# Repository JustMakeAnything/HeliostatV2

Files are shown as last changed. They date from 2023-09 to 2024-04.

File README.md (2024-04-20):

# Heliostat V2
Files for my Heliostat project. The hardware consists of an ESP32 which is connected to two stepper motors to control the azimuth and elevation of a mirror and 4 switches to detect the endpoints for the motors. Further hardware is currently not supported.

## Instructable
For details see the Instructable at:

[Instructables](https://www.instructables.com/Heliostat-Reflects-Sunlight-Inside/)

## Design

The software uses [ESPHOME](https://esphome.io/) to create the firmware. It is autonomous after it was configured especially to a specific target location (angles) where the mirror should reflect to. There is a web interface to see some values and trigger a motor calibration as well as buttons to set the target. The values are stored in the eeprom of the ESP32.

## ESPHome

These main folder is for the esphome files. Compile and upload them from the command line with:

**esphome run .\code\heliostat.yaml**

To your ESP32. See [Esphome](https://esphome.io/) for details. I haven't tested integration with home assistant. It is not needed to run the heliostat.

### Configuration

To connect to your wifi, you need to adapt the secrects.yaml. Wifi is needed to get the exact time. You can also access the web interface at heliostat.local of the given network to set the target during runtime. Otherwise use the constants.yaml to set an initial target.
There is an experimental [autocalibration](./docs/autocalibration.md) available when an additional light sensor is mounted.

## 3D Print

The STL files for 3D Print are in folder 3DPrint

There is a subfolder STL for the STL files
The folder SolidEdgeParts contains the design files for Solid Edge. Since the parts are usually exposed to the sun it makes sense to print them in a material which is more heat resistant than PLA. Especially the parts with mechanical stress like the cogweels tend to deform when in the sun. I have used transparent PETG.

### 3D Print settings

The parts can be printed with standard settings. You should rotate the parts to the flat side when slicing. Some parts like the axle and the SideNoMotor need supports.

## Electronics

Although the electronics is not complicated, you should have some experience in soldering and ideally done an ESP project before.

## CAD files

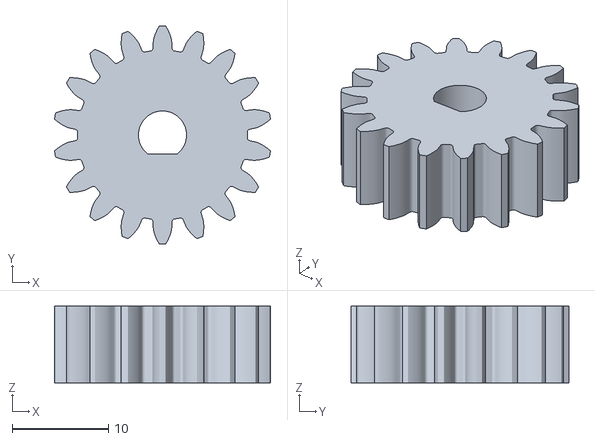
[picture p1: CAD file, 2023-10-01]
3DPrint/STL/basepinion.stl
22.5 x 22.7 x 8.00

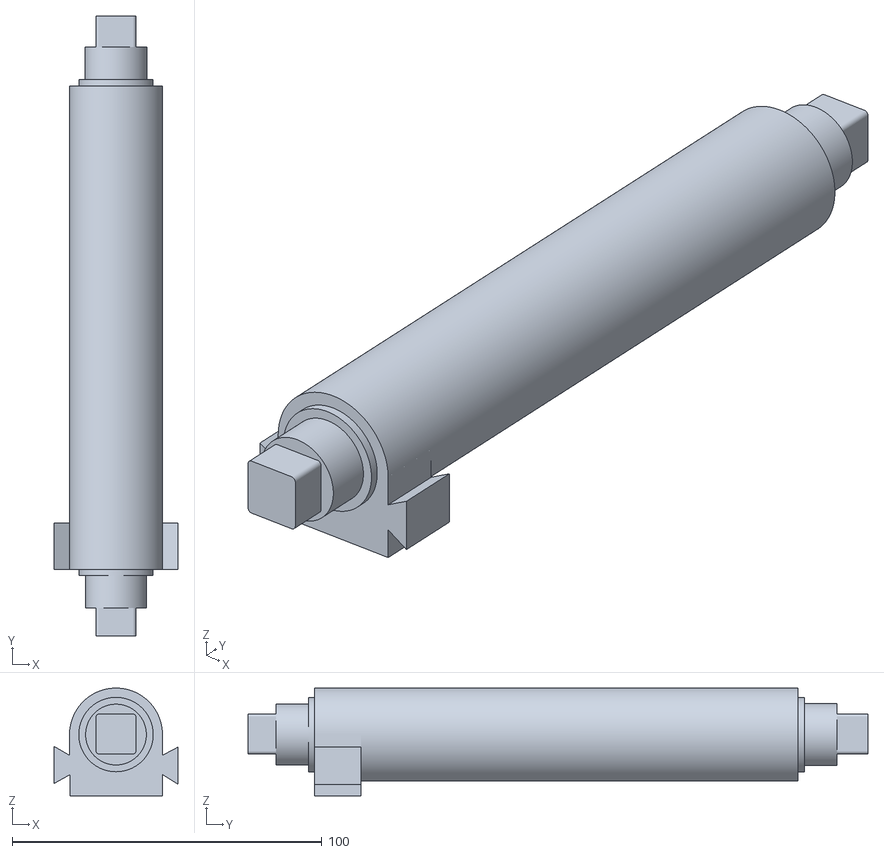
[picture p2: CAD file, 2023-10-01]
3DPrint/STL/Axle.stl
40.0 x 200.0 x 34.8

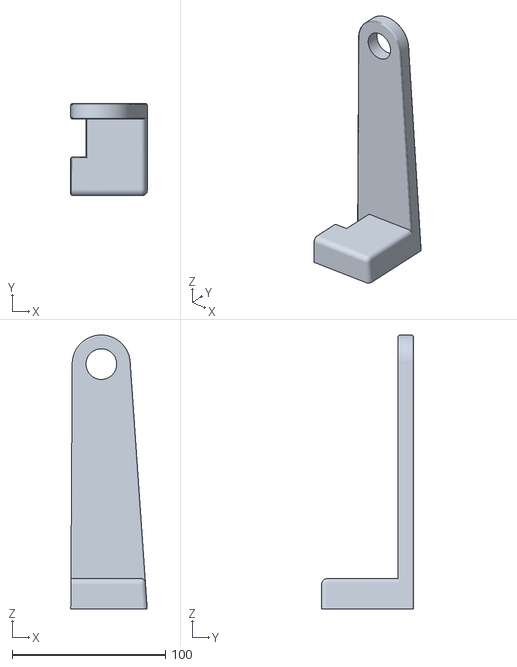
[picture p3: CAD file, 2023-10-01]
3DPrint/STL/SideNoMotor.stl
50.0 x 60.0 x 179.0

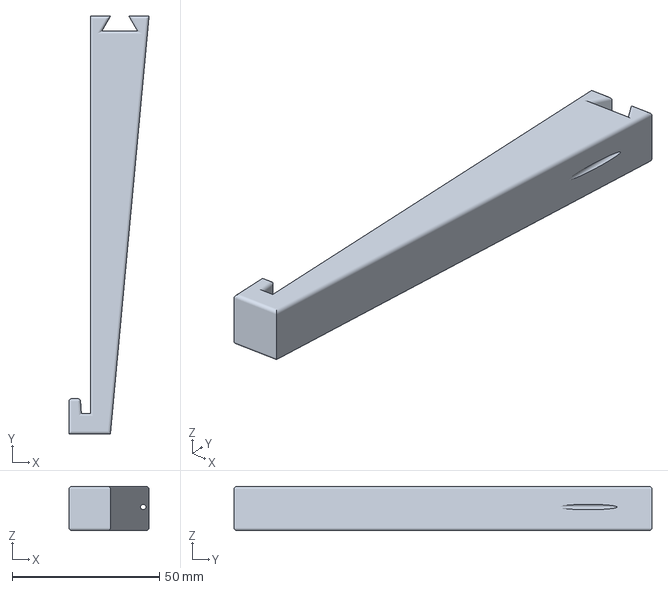
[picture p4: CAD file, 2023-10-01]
3DPrint/STL/Holder.3mf
27.3 x 142.0 x 15.0 mm

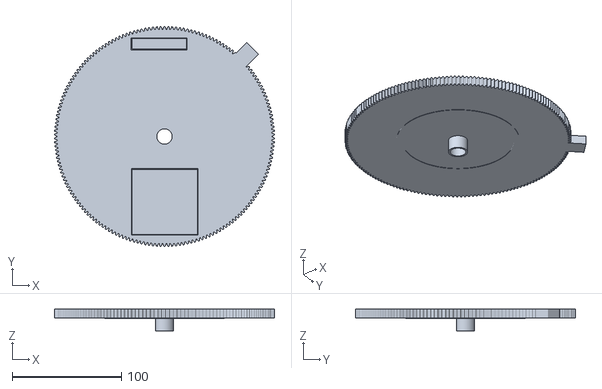
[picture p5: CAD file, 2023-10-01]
3DPrint/STL/basegear.stl
201.8 x 201.8 x 20.0

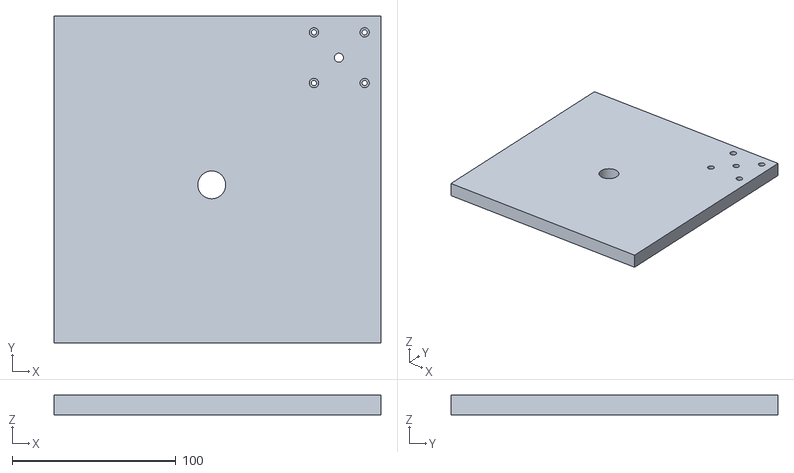
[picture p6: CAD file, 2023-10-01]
3DPrint/STL/Lid.stl
200.0 x 200.0 x 12.0

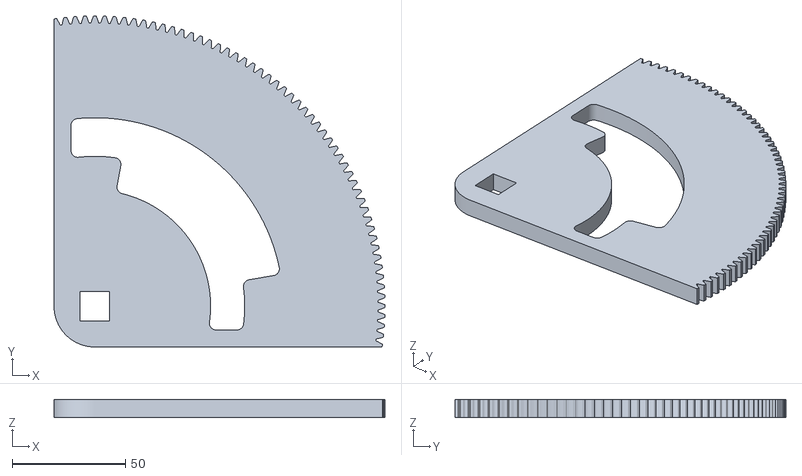
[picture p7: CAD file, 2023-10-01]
3DPrint/STL/SideGear.stl
145.8 x 145.8 x 8.00

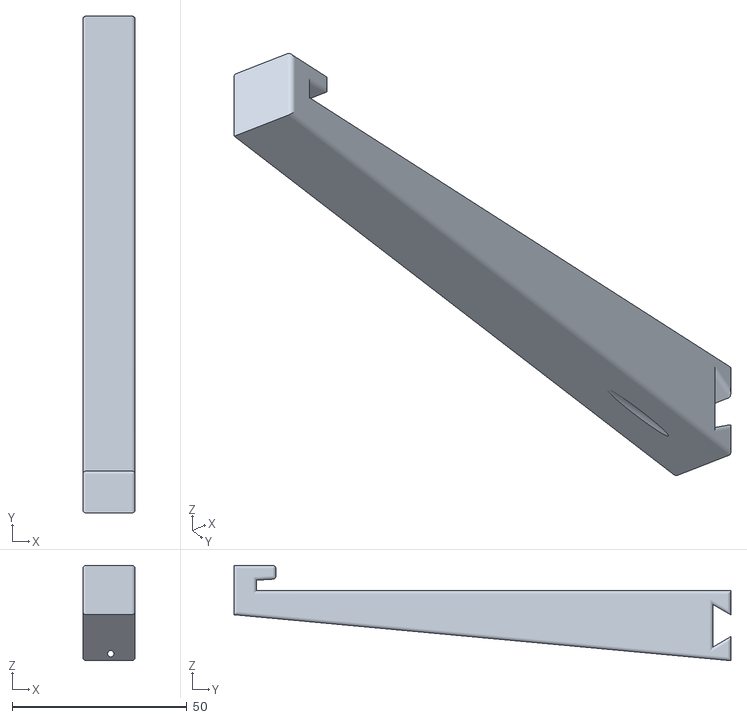
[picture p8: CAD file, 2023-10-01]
3DPrint/STL/Ausleger.stl
15.0 x 142.0 x 27.3

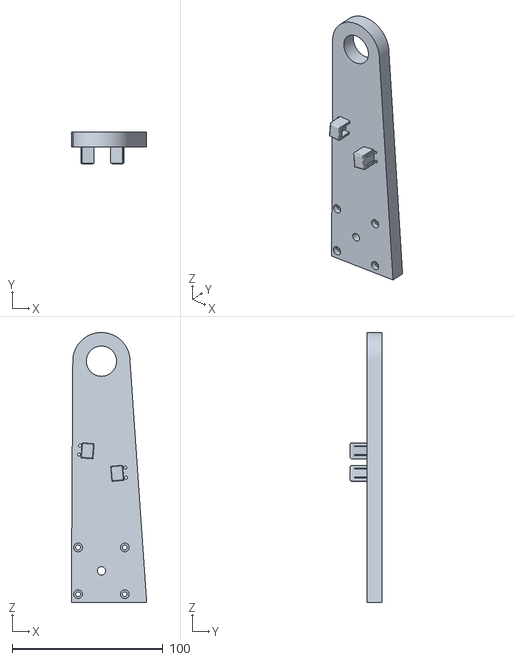
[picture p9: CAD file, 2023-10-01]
3DPrint/STL/SideMotor.stl
50.0 x 21.0 x 179.0

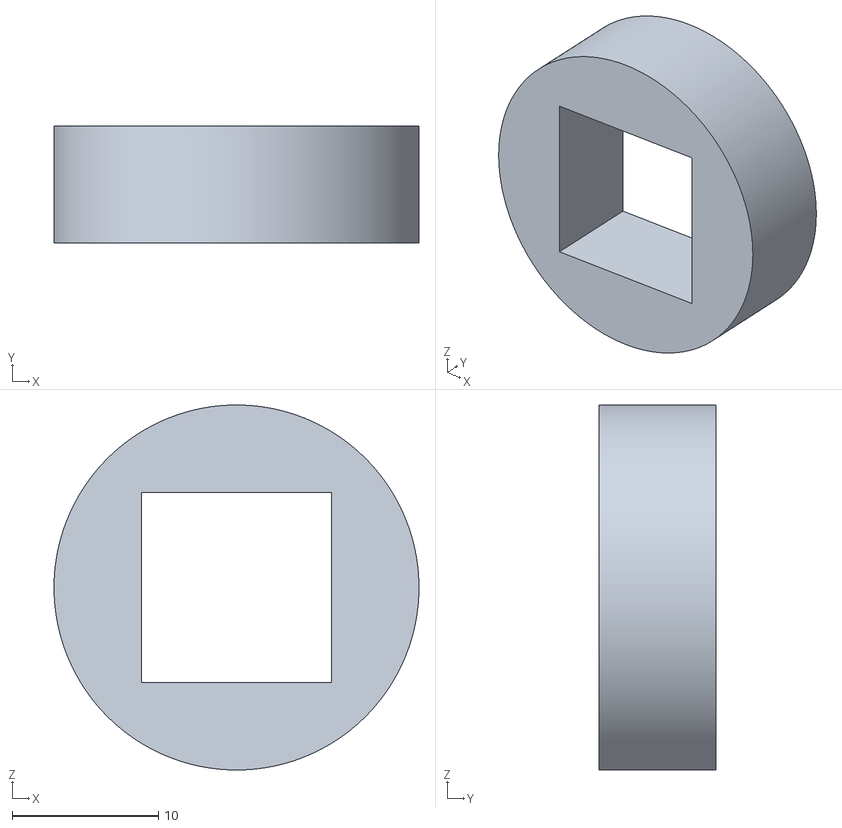
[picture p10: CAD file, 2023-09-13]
3DPrint/STL/Endplug.stl
25.0 x 8.00 x 25.0

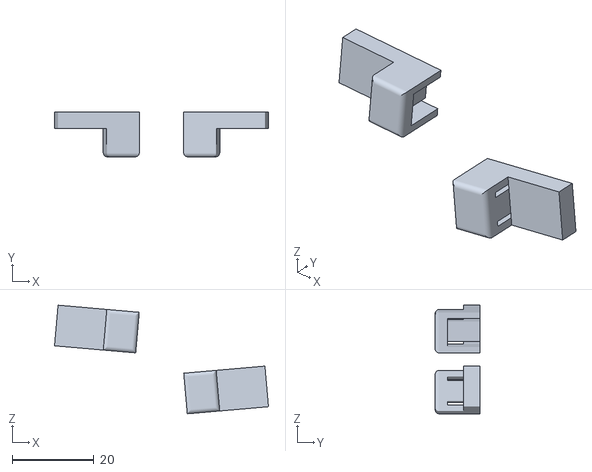
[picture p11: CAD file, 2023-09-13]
3DPrint/STL/Endstop.stl
52.5 x 11.0 x 26.6

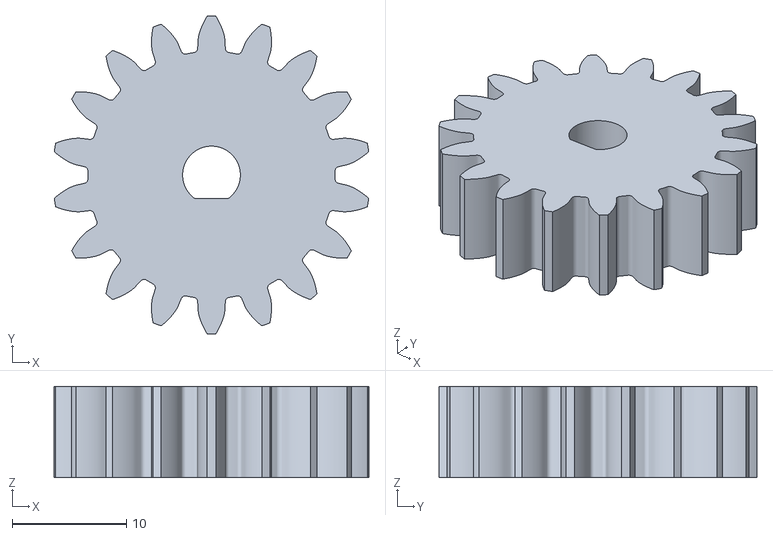
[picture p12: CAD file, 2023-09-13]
3DPrint/STL/sidepinion.stl
27.5 x 27.8 x 8.00

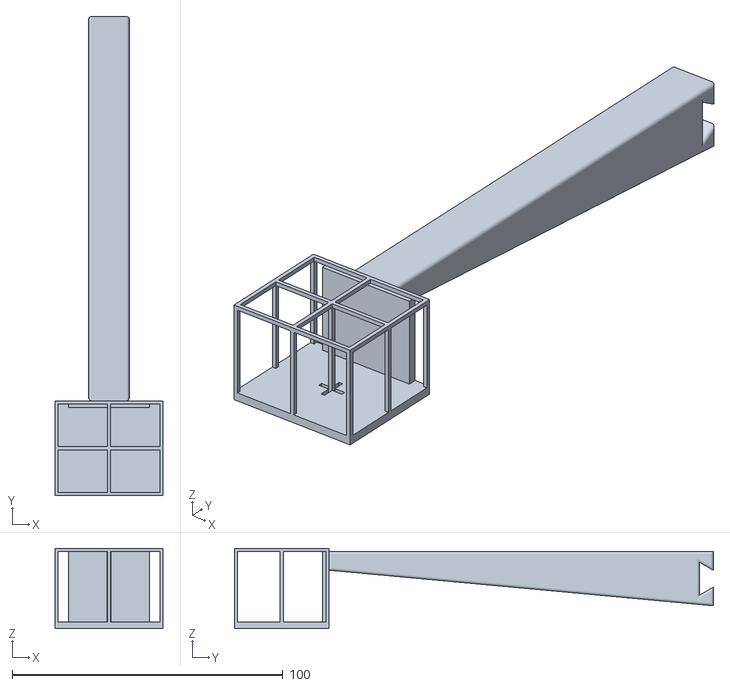
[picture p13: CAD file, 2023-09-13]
3DPrint/STL/HolderTargetSun.stl
40.0 x 177.0 x 29.6

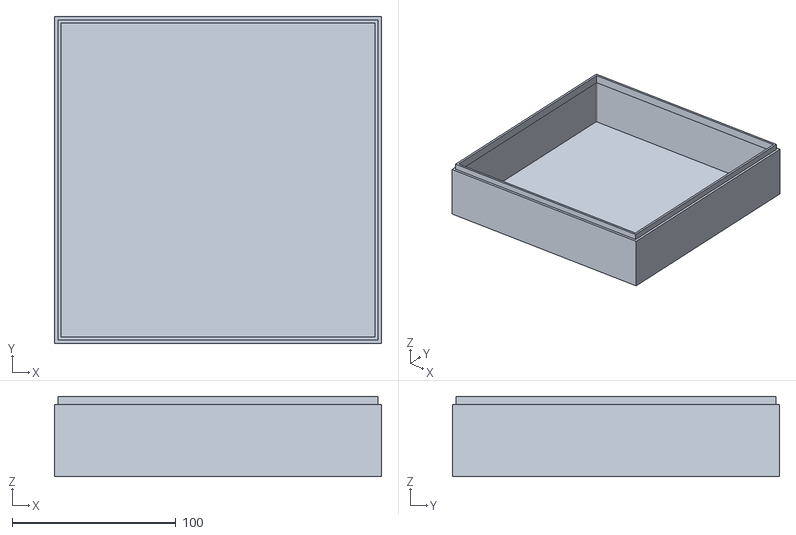
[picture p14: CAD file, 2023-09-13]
3DPrint/STL/Box.stl
200.0 x 200.0 x 49.0

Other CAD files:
3DPrint/Old/Arm.stl
3DPrint/Old/Axis.stl
3DPrint/Old/SideGear.stl
3DPrint/Old/Lid.stl
3DPrint/Old/Side1.stl
3DPrint/Old/Side2.stl
3DPrint/Old/basegear1.stl
3DPrint/Old/basepinion1.stl
3DPrint/Old/gearstopper.stl
3DPrint/STL/Holder.stl

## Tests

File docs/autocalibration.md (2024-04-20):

# Autocalibration

When a light sensor is mounted, the system can help with the calibration. Therefore the system checks if enough sunlight is available since it will not work on cloudy days due to too much ambient light and no directed light to determine a direction. A measurement is done every hour configurable in **calculations.h sunsearchdelay**

When enough light is available, the mirror and sensor is moved into the sun and tries to determine the exact direction of the sunlight. This is done by moving in a spiral around the supposed direction and measure the sunlight in the tube with the light sensor at the end. The center of the spiral also drifts in the direction where most light was measured. This process ends when the ambient sunlight falls under a certain level (no direct sunlight anymore) or the maximum search range is analyzed and no value higher than 94% of the ambient light was detected. The duration of the process is limited to 500 steps. with approx. 10 rotations. when no new measurement with a higher value is found afer 150 steps, the measurement is ended early successfully.

The direction of the maximum value is then stored as sun direction. It is stored as steps of the motors. When the three values are stored, the system attempts to calculate an adapted configuration. This will be repeated with the following measurements of the same day increasing the precision. No measurements over multiple days are stored or used. The values are shown in the log or webui.

Currently the system is not adjusting the values automatically since it is still alpha.

[12:00:56][I][measure:440]: amb: 3.069250 dir: 2.959000 saz: 0 sel: 1      driftaz -232 driftel: 20 maaz: 532 taaz: 764    az 149°
[13:38:45][I][measure:440]: amb: 2.953625 dir: 1.730625 saz: 62 sel: -85   driftaz -221 driftel: 34 maaz: 1317 taaz: 1538  az 185°
[15:19:50][I][measure:440]: amb: 2.989750 dir: 1.623750 saz: 0 sel: 1      driftaz 293 driftel:   2 maaz: 2301 taaz: 2301  az 221°
[16:59:47][I][measure:440]: amb: 2.943500 dir: 2.208625 saz: -75 sel: -103 driftaz 380 driftel: -25 maaz: 3260 taaz: 2867  az 247°

36° = 774
72° = 1537 / 2 = 769
26° = 566   * 36 / 26 = 783

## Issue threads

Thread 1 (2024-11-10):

Axel stl file issue

ecasas6, 2024-11-10:
I'm following along with your project, cool idea.  I was looking at the 3d files and it looks like you uploaded an incomplete version of the axel.stl file.  The one uploaded, only has the insertion points for the ausleger on one side.  The axel in your video shows the insertion points in the middle and on the opposite side.

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

JustMakeAnything, 2024-11-10:
Hello Edgar,

Thanks for your isssue report. This file is indeed not the intended one. I fixed it and pushed the correct one.

Best regards,
Martin

ecasas6, 2024-11-10:
Thank you :)

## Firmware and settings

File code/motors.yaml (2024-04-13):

globals:
  - id: minElevation
    type: float
    restore_value: no
    initial_value: ${MinElevation}
  - id: maxElevation
    type: float
    restore_value: no
    initial_value: ${MaxElevation}
  - id: minAzimuth
    type: float
    restore_value: no
    initial_value: ${MinAzimuth}
  - id: maxAzimuth
    type: float
    restore_value: no
    initial_value: ${MaxAzimuth}
  # - id: motorel_prev
  #   type: float
  #   restore_value: no

  # tilt
  - id: tiltmiddle
    type: float
    restore_value: no
    initial_value: ${tiltMiddle}
  - id: tiltangle
    type: float
    restore_value: no
    initial_value: ${tiltAngle}


stepper:
  - platform: a4988
    id: stepper_el
    step_pin: GPIO27
    dir_pin: GPIO12
    max_speed: 300 steps/s
    sleep_pin:
      number: GPIO26
      inverted: true    
    acceleration: 80 steps/s^2
    deceleration: 120 steps/s^2
    sleep_when_done: true

  - platform: a4988
    id: stepper_az
    step_pin: GPIO33
    dir_pin: GPIO25
    max_speed: 400 steps/s
    sleep_pin: 
      number: GPIO32
      inverted: true
    acceleration: 80 steps/s^2
    deceleration: 150 steps/s^2
    sleep_when_done: true


sensor:
  - platform: template
    name: "Motor Elevation"
    id: "motorel"

  - platform: template
    name: "Motor Azimuth"
    id: "motoraz"


script:
  # Update mirror position
  - id: updatemirror
    then:
      - lambda: |-
          calculateAngles();
          updateStatus();
          motorcontrol();

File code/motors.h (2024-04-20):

// Copyright 2024

int setMotor(float motorPos, float min, float max, int limit) {
    if (motorPos < 0) {
        motorPos += 360.0f;
    }
    motorPos = (motorPos - min) / (max-min) * static_cast<float>(limit);
    // ESP_LOGI("calculation", "Motor Stepper: %f",motorPos);
    // ESP_LOGI("calculation", "MinAzimuth Stepper: %f",id(minAzimuth));
    // ESP_LOGI("calculation", "MaxAzimuth Stepper: %f",id(maxAzimuth));
    // ESP_LOGI("calculation", "Right Limit: %d",id(west_limit));
    if (motorPos > 0 && motorPos < limit) {
        return motorPos;
    }
    return -1;
}

bool capmotorbounds(int &motorsteps, int boundary) {
    if (motorsteps < 0) {
        motorsteps = 0;
        return false;
    }
    if (motorsteps > boundary) {
        motorsteps = boundary;
        return false;
    }
    return true;
}

float motorToAngle(int motorPos, float min, float max, int motorsteps) {
    // min, max = angles limt = motorsteps
    float angle = motorPos / static_cast<float>(motorsteps);
    angle = (angle * max - min) + min;
    // ESP_LOGI("calculation", "Motor Stepper: %f",motorPos);
    if (angle < 0) {
        angle += 360.0f;
    }
        return angle;
}

void setelevation(int steps) {
    id(stepper_el).set_target(steps);
}
void setazimuth(int steps) {
    id(stepper_az).set_target(steps);
}

int roundToMicrostep(int motorPos) {
    int motorValue = motorPos;
    // microsteps;
    return ( motorValue / microsteps ) * microsteps;
}

int toMicrostep(int motorPos) {
    int motorValue = motorPos;
    // microsteps;
    return motorValue * microsteps;
}

float adjustel(float motoraz_act, float motorel_act) {
    // when heliostat is tilted, adjust the elevation according to the tilt angle
    float tiltdirection = motoraz_act - id(tiltmiddle);
    float eladjustment = cos(to_rad(tiltdirection)) * id(tiltangle);

    // ESP_LOGI("motor", "mel: %f maz: %f tiltdir: %f eladjust: %f",
    //     motorel_act, motoraz_act, tiltdirection, eladjustment);

    return motorel_act + eladjustment;
}

void motorcontrol() {
    if ((id(allValid) == false) || (id(measuresun) == true) || (id(tracksun) == true)) {
        return;
    }
    //
    // Execution when both values are in range, otherwise do nothing
    //
    // When elevation goes downwards, there is some clearance in the gears
    // Fix this by subtracting a fixed value from the elevation
    //
    // float motorel_act = id(motorel).state;
    // float motorel_corr = id(motorel).state;
    // float motoraz_act = id(motoraz).state;
    // // when heliostat is tilted, adjust the elevation according to the tilt angle
    // float tiltdirection = motoraz_act - id(tiltmiddle);
    // float eladjustment = cos(to_rad(tiltdirection)) * id(tiltangle);

    // ESP_LOGI("motor", "mel: %f maz: %f tiltdir: %f eladjust: %f",
    //     motorel_act, motoraz_act, tiltdirection, eladjustment);

    float motoraz_act = id(motoraz).state;
    float motorel_corr = adjustel(motoraz_act, id(motorel).state);

    // float motorel_corr = motorel_act;
    // if (motorel_act < id(motorel_prev)) {
    // // Going down
    //     motorel_corr -= 0.9;
    // }
    // Keep this motorel for the next call when it changed due to call to 'calculatetarget'
    // id(motorel_prev)= id(motorel).state;
    //
    //
    int targetEl = setMotor(motorel_corr, id(minElevation), id(maxElevation), static_cast<float>(id(upper_limit)));
    int targetAz = setMotor(motoraz_act , id(minAzimuth),   id(maxAzimuth),   static_cast<float>(id(west_limit)));
    // ESP_LOGI("isnan", "el: %f",motorel_corr);
    // ESP_LOGI("isnan", "az: %f",id(motoraz).state);
    // ESP_LOGI("isnan", "tel: %f",targetEl);
    // ESP_LOGI("isnan", "taz: %f",targetAz);
    if ((isnan(motorel_corr) == false) && (isnan(id(motoraz).state) == false)) {
        id(calculated) = true;
    }
    if (targetEl == -1 || targetAz == -1) {
        ESP_LOGI("motor", "out of bounds of motors");
        return;
    }
    targetEl = roundToMicrostep(targetEl);
    targetAz = roundToMicrostep(targetAz);
    setelevation(targetEl);
    setazimuth(targetAz);
}

int getelevation() {
    return id(stepper_el).current_position;
}
int getazimuth() {
    return id(stepper_az).current_position;
}

void reportelevation(int steps) {
    id(stepper_el).report_position(steps);
}
void reportazimuth(int steps) {
    id(stepper_az).report_position(steps);
}

void movemotorazrelative(float anglechange) {
    id(motoraz).state += anglechange;
    motorcontrol();
}

void movemotorelrelative(float anglechange) {
    id(motorel).state += anglechange;
    motorcontrol();
}

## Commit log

2023-10-01 New 3D print files, restructuring (V2.1)
    [Arm.stl, Ausleger.stl, AuslegerZielkreuz.stl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]
2024-04-01 Complete redesign and cleanup
    [calibration.yaml, motors.yaml]
2024-04-03 Prepare for Suncalibration
    [calibration.yaml, suncalibration.yaml]
2024-04-07 Autocalibration with additional light sensor
    [calibration.yaml, motors.yaml, suncalibration.yaml]
2024-04-11 Before Fix
    [suncalibration.yaml]
2024-04-13 Added manual mode, refactorings
    [motors.yaml]
2024-04-20 Added a continious sun tracking function
    [suncalibration.yaml]
2024-11-10 Fix Axle STL
    [Axle.stl]
2025-10-12 Fixed bootup and calibration issue
